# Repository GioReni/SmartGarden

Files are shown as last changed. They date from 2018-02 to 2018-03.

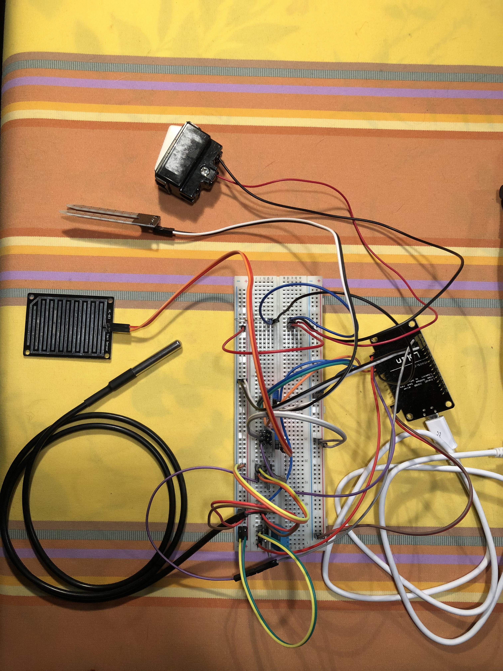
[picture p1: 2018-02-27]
foto/UnitaSensori.jpg

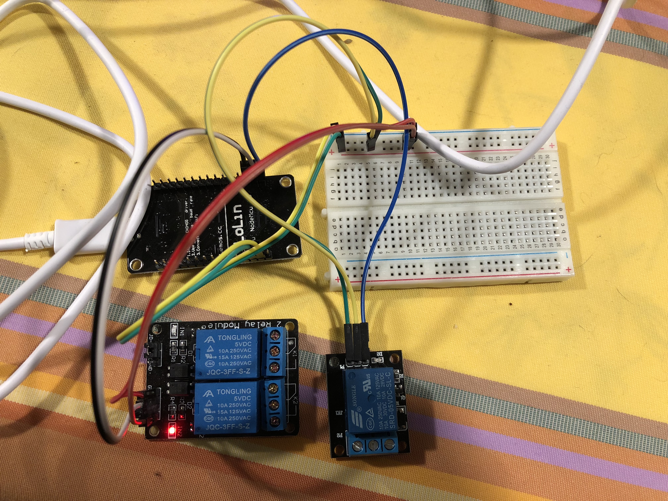
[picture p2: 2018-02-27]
foto/UnitaAttuatori.jpg

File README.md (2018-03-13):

# Progetto SmartGarden - Corso Sistemi Embedded (Università degli Studi di Milano, Anno Accademico 2017-2018)

## Autori:
Alessandro Gigliotti, Giovanni Reni 
## Board utilizzate:
NodeMCU ESP8266

### Descrizione generale:
In questo progetto, abbiamo realizzato un sistema di gestione intelligente di un piccolo orto o giardino. È presente un impianto d'irrigazione, basato sul controllo di ciò che accade e quindi di come si modifica, l'ambiente circostante. L'impianto entra infatti autonomamente in azione, quando si verificano determinate condizioni (come secchezza del terreno o assenza di pioggia), tenendo costantemente sotto controllo varie informazioni sull'aria, terra, meteo e sullo stato degli strumenti d'irrigazioni utilizzati. L'irrigazione può entrare in funzione, utilizzando una cisterna che raccoglie l'acqua piovana, oppure tramite un impianto idraulico. È altresì possibile attivare l'irrigazione anche manualmente da un utente tramite un pulsante fisico.
Le informazioni rilevate tramite i sensori in giardino, vengono inviate e visualizzate su un display, attaccato ad un'altra board, posizionato in un luogo chiuso (ad esempio in casa). Affianco al display, ci saranno anche 4 led, che segnalano la presenza/assenza di pioggia, la presenza/assenza di sole, lo stato del serbatoio pieno o vuoto. Ci sono infine 3 pulsanti fisici, posizionati accanto al display, per azionare manualmente l'irrigazione, per accendere una lampada per illuminare e un tasto per arrestare entrambe queste attività.
Inoltre il sistema sfrutta un'applicazione mobile, dalla quale sono consultabili tutte le informazioni lette dai sensori e lo stato della cisterna. Sono presenti inoltre 3 pulsanti virtuali, gemelli di quelli fisici, per azionare gli strumenti del progetto da un dispositivo. Infine l'app invia anche notifiche, relative agli eventi che accadono nel sistema.

### Descrizione dettagliata:
All'esterno, avremo il primo nodeMCU posto in prossimità del giardino. Ad esso, sono attacati tutti i sensori che utilizziamo per recepire le informazioni chiave che andremo ad utilizzare per il funzionamento generale del progetto.
I sensori utilizzati da questo nodeMCU sono:
- Temperatura e umidità dell'aria
- Temperatura e umidità della terra
- Rilevazione della pioggia
- Fotoresistore

Queste informazioni verranno costantemente tenute sotto controllo dal primo nodeMCU (file UnitaSensori.ino), che le invierà periodicamente ad un altro nodeMCU (definiamolo d'ora in avanti "controllore"), che sarà in un luogo chiuso, quindi idealmente all'interno della casa.
Le informazioni rilevate, in costante aggiornamento, saranno anche consultabili da un dispaly interno alla casa e dall'applicazione mobile.

Vicino al giardino, sarà presente una cisterna che raccoglie l'acqua piovana, che verrà usata per irrigare il giardino, nel caso in essa sia presente una sufficiente quantità d'acqua. Se la cisterna fosse vuota, il giardino verrà allora irrigato direttamente con l'acqua dell'impianto idraulico casalingo.

Tutte le decisioni, su come e quando irrigare, sono prese quindi dal nodeMCU "controllore" (file UnitaDiControllo) che abbiamo posizionato internamente alla casa e che è in comunicazione con il primo nodeMCU (UnitaSensori) di cui abbiamo parlato sopra, tramite il protocollo UDP, via WI-FI. In base alle informazioni che arrivano al controllore, quest'ultimo deciderà se azionare o meno l'irrigazione, ed in caso positivo, se sfruttare la cisterna o l'impianto idraulico casalingo. 

Abbiamo poi un terzo ed ultimo nodeMCU (UnitaAttuatori), all'esterno, a cui sono attaccati 3 relays:
- Uno per attivare l'elettrovalvola che aziona l'impianto idraulico casalingo per irrigare
- Uno per aprire la valvola dell'acqua della cisterna, per irrigare
- Uno per accendere una lampada per illuminare una pianta (quest'ultimo è azionabile solo manualmente)

Anche questo nodeMCU (UnitaAttuatori), sarà gestito dal controllore, grazie alle informazioni derivanti dal primo nodeMCU (UnitaSensori).

Descriviamo più dettagliamente il nodeMCU "controllore" (UnitaDiControllo), che sta in casa:

Esso ogni n secondi, riceve dal primo nodeMCU che controlla i sensori, i dati che ha letto.
Il controllore riceve ed elabora quindi i dati, e decide se azionare o meno i relays del terzo nodeMCU (UnitaAttuatori).
Attaccati a questo nodeMCU "controllore", abbiamo:
- Uno schermo LCD, sul quale possiamo visualizzare i dati letti dal primo nodeMCU (UnitaSensori), quindi: temperatura e umidità dell'aria, temperatura della terra, l'umidità della terra (terreni arido o umido) e infine lo stato acceso/spento dell'irrigazione e della luce della lampada.
- Quattro led: uno di colore blu, che segnala la presenza (acceso) o assenza (spento) di pioggia (funziona tramite sensore di pioggia), uno di colore giallo, che segnala la presenza (acceso) o assenza (spento) della luce del sole (funziona tramite fotoresistore), uno di colore verde, che si accende solamente quando la cisterna è piena, e uno di colore rosso che si accende solamente quando la cisterna è vuota.
un'altro, che può assumere i colori verde e rosso: verde nel caso la cisterna sia piena d'acqua, e rosso nel caso sia vuota.
- Tre bottoni: essi, fanno scattare i relays del nodeMCU esterno (UnitaAttuatori). Un bottone comanda l'apertura dell'irrigazione, uno l'accensione della lampada e l'ultimo l'arresto di entrambe queste attività.

Infine, abbiamo utilizzato un'applicazione per visualizzare le informazioni lette dal nodeMCU esterno (UnitaSensori), su un dispositivo mobile, sia Android che iOS. L'applicazione si chiama Blynk, ed è scaricabile gratuitamente dal sito https://www.blynk.cc/ e lavora con varie piattaforme, tra cui ESP8266.
Da questa applicazione mobile, una volta installata e impostato il progetto SmartGarden, sono consultabili due diversi tab.
Nel primo, chimato "sensori", sono consultabili tutte le informazioni lette dai sensori: temperatura, umidità dell'aria e temperatura della terra, attraverso delle barre circolari, con al centro il valore rilevato. Inoltre c'è un piccolo led che quando è acceso, ci informa che la cisterna è piena d'acqua.
Nel secondo tab, chiamato "relays", sono invece presenti 3 pulsanti virtuali, che assolvono alle stesse funzionalità dei pulsanti fisici gemelli, attaccati al nodeMCU controllore. Questi 3 pulsanti, una volta premuti, possono quindi far attivare l'irrigazione, accendere la lampada ed uno per eventualmente fermare queste due attività se necessario, direttamente dal proprio dispositivo mobile, sfruttando l'applicazione.
Infine quest'applicazione invia delle utili notifiche a tutti i dispositivi che la installano, se connessi con il progetto, quando si verifica l'accensione dell'impianto di irrigazione o della lampada, o l'eventuale stop di tutte le attività. Sarà così possibile vedere tramite la notifica, ad esempio l'orario a cui si è accesa l'irrigazione in maniera automatica, direttamente dal proprio dispositivo. 

### Lista completa componenti utilizzati:
- 1 Sonda sensore di temperatura waterproof DS18B20
- 1 Rain sensor HL38
- 1 Modulo sensore umidità terra - igrometro YL-69
- 1 KY-018 modulo Fotodiodo
- 1 Elettrovalvola
- 1 Interruttore a galleggiante sensore livello liquido di accio inox RG-1075S
- Pompa acqua 220V
- 1 5V 1-Channel Relay Module
- 1 5V 2-Channel Relay Module
- 3 Pulsanti
- 1 resistenza da 100 Ohms
- 1 resistenza da 220 Ohms
- 1 resistenza da 1 kOhm
- 1 resistenza da 4.7 kOhms
- 5 resistenze da 10 kOhms
- 4 LED (Red, Green, Blue, Yellow)
- 1 KY-015 Sensore di temperatura e umidità dell'aria (DHT11)
- 1 Modulo LCD 20x4 I2C/TWI

## Lista librerie utilizzate:
- Blynk Library (app: https://github.com/blynkkk/blynk-library/releases/tag/v0.5.1)
- ESP8266WiFi
- WiFiUdp
- LiquidCrystal_I2C
- SimpleTimer
- SPI
- Adafruit_Sensor
- DHT
- DHT_U
- OneWire
- DallasTemperature

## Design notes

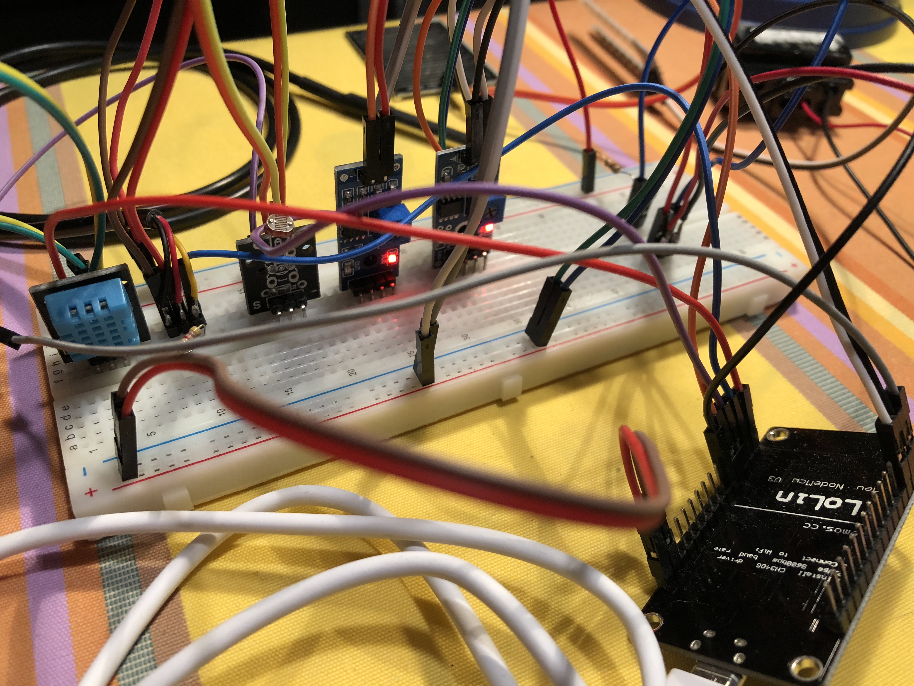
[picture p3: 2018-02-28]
foto/UnitaSensori2.jpg

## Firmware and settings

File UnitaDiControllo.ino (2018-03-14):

/*
 *  Copyright 2018 Giovanni Reni & Alessandro Gigliotti
 * 
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
 * SmartGarden1.0 is distributed in the hope that it will be useful,
 * but WITHOUT ANY WARRANTY; without even the implied warranty of
 * MERCHANTABILITY or FITNESS FOR A PARTICULAR PURPOSE. See the
 * GNU General Public License for more details.
 * You should have received a copy of the GNU General Public License
 * along with this program. If not, see <http://www.gnu.org/licenses/>.
 */

#define BLYNK_PRINT Serial

#include <ESP8266WiFi.h>
#include <WiFiUdp.h>
#include <LiquidCrystal_I2C.h>
#include <SimpleTimer.h>
#include <SPI.h>
#include <BlynkSimpleEsp8266.h>

LiquidCrystal_I2C lcd(0x3F, 20, 4);

char auth[] = "****"; //Blynk app

WiFiUDP Udp;
unsigned int localUdpPort = 4210;                 //cambiare con porta che si vuole assegnare a questo NodeMcu (UnitaDiControllo)
char incomingPacket[UDP_TX_PACKET_MAX_SIZE];

IPAddress ip(192, 168, 1, 35);                     //cambiare con indirizzo IP che si vuole assegnare a questo NodeMcu (UnitaDiControllo)
IPAddress gateway(192, 168, 1, 254);               //cambiare con gateway della propria rete
IPAddress subnet(255, 255, 255, 0);                //cambiare con subnet della propria rete

const char* ssid = "ArduinoAfternoon";                     //cambiare con ssid della propria Wi-Fi
const char* password = "***";                 	   //cambiare con password della propria Wi-Fi

char * luceOff = "L0";                            //comando spegni luce
char * luceOn = "L1";                             //comando accendi luce
char * pumpOff = "P0";                            //comando spegni pompa
char * pumpOn = "P1";                             //comando accendi pompa
char * evOff = "E0";                              //comando spegni elettrovalvola
char * evOn = "E1";                               //comando accnedi elettrovalvola

int tempoIrrPuls = 10;                            //cambiare a piacere se si vuole modificare tempo (in sec.) innaffiata con pulsante
int tempoIrrAuto = 300; //300 sec <--> 5 min      //cambiare a piacere se si vuole modificare tempo (in sec.) innaffiata automatica
int tempoLucePuls = 10;                           //cambiare a piacere se si vuole modificare tempo (in sec.) illuminazione con pulsante
int tempoLuceAuto = 300;                          //cambiare a piacere se si vuole modificare tempo (in sec.) illuminazione automatica

//indirizzo IP + Porta NodeMcu ATTUATORE
char * indirizzoRelaisGiardino = "192.168.1.36";  //cambiare con indirizzo IP del proprio NodeMcu attuatore
int portaRelaisGiardino = 4240;                   //cambiare con porta del proprio NodeMcu attuatore

//pin LED pioggia
int pinGiallo = D5;
int pinBlu = D6;

//pin LED serbatoio
int pinVerde =  D4;
int pinRosso = D7;

//pin bottone lucePianta
int bottoneLuce = D8;

//pin bottone pompa
int bottonePompa = D0;

//pin bottone STOP
int bottoneStop = A0;

//variabile pioggia (0 --> NON piove)
int pioggia = 0;
//variabile serbatoio (0 --> vuoto)
int serbatoio = 0;
//variabile umidita' terra
int umiditaTerra;
//variabile temperatura terra
double temperaturaTerra;
//variabile temperatura aria
int temperatura;
//variabile luce env.
int luce;
//variabile umidita aria
int umidita;
//variabile tipo irrigatore
char irrigatore [] = "P";
//variabile tipo luce
char illuminazione [] = "L";
//variabile pulsante irrigazione temporanea
int letturaPulsanteAcqua = LOW;
//variabile pulsante illuminazione temporanea
int letturaPulsanteLuce = LOW;
//variabile pulsante STOP
int letturaPulsanteStop = 0;
//variabile comando
char comando [UDP_TX_PACKET_MAX_SIZE];
//variabile per convertire gli interi
char temp [15];
//variabile temporanea numero
int numero;


//######################################################################################## FUNCTIONS 1 ########################################################################################
void printIllOff() {
  lcd.setCursor(0,3);
  lcd.print("Luce:");
  lcd.print("OFF   ");
}

void printAcquaOff() {
  lcd.setCursor(11,3);
  lcd.print("Acqua:");
  lcd.print("OFF");
}

void printIllIrrOff() {
  printIllOff();
  printAcquaOff();
}


//########################################################################################### SETUP ###########################################################################################
void setup() {
  //pin LED pioggia
  pinMode(pinGiallo, OUTPUT);
  pinMode(pinBlu, OUTPUT);

  //pin bottoni STOP, IRRIGAZIONE, LUCE
  pinMode(bottonePompa, INPUT);
  pinMode(bottoneStop, INPUT);
  pinMode(bottoneLuce, INPUT);
  
  //pin LED serbatoio
  pinMode(pinVerde, OUTPUT);
  pinMode(pinRosso, OUTPUT);

  Blynk.begin(auth, ssid, password);
  
  Serial.begin(9600);
  Serial.println();
  Serial.printf("Connecting to %s ", ssid);
  //WiFi.mode(WIFI_STA);
  WiFi.config(ip, gateway, subnet);
  WiFi.begin(ssid, password);
  while (WiFi.status() != WL_CONNECTED)
  {
    delay(500);
    Serial.print(".");
  }
  Serial.println(" connected");

  //Serial.print("Indirizzo IP UnitaDiControllo: ");
  //Serial.pritnln(WiFi.localIP());
  Udp.begin(localUdpPort);
  Serial.printf("Now listening at IP %s, UDP port %d\n", WiFi.localIP().toString().c_str(), localUdpPort);

  //settaggio display LCD
  lcd.begin(20,4);
  lcd.init();
  lcd.backlight();

  printIllIrrOff();
}


//######################################################################################## FUNCTIONS 2 ########################################################################################
void sendPacket(char pacchetto [8], char * indirizzo, int porta) {
  Udp.beginPacket(indirizzo, porta);
  Udp.write(pacchetto);
  Udp.endPacket();
}

void printTemp(int i) {
  lcd.setCursor(0,0);
  lcd.print("Temp:");
  lcd.print(String(i));
  lcd.print((char)223);
  lcd.print("C");
}

void printHum(int i) {
  lcd.print("  Umid:");
  lcd.print(String(i));
  lcd.print("%");
}

void printTempTerra(double d) {
  lcd.setCursor(0,1);
  lcd.print("Temp Terra:");
  lcd.print(String(d));
  lcd.print((char)223);
  lcd.print("C");
}

void printUmidTerra(int i) {
  lcd.setCursor(0,2);
  if(i==1) {
     lcd.print("Terreno Umido");
   }
   else if(i==0) {
     lcd.print("Terreno Arido");
   }
}

void ledPioggia(int i) {
  if(i==1) {
     digitalWrite(pinBlu, HIGH);
     analogWrite(pinGiallo, LOW);
   }
   else if(i==0) {
     digitalWrite(pinBlu, LOW);
     analogWrite(pinGiallo, HIGH);
   }
}

void ledSerbatoio(int i) {
  if(i==0) {
    digitalWrite(pinVerde, LOW);
    digitalWrite(pinRosso, HIGH);
   }
   else {
     digitalWrite(pinVerde, HIGH);
     digitalWrite(pinRosso, LOW);
   }
}

void spegniTutto() {
  sendPacket(luceOff, indirizzoRelaisGiardino, portaRelaisGiardino);
  sendPacket(pumpOff, indirizzoRelaisGiardino, portaRelaisGiardino);
  sendPacket(evOff, indirizzoRelaisGiardino, portaRelaisGiardino);
}

void clearArray(char lista[UDP_TX_PACKET_MAX_SIZE]) {
  for (int i = 0; i< sizeof(lista); i++) {
    lista[i]=(char)0;
  } 
}

void printIllOn() {
  lcd.setCursor(0,3);
  lcd.print("Luce:");
  lcd.print("ON    ");
}

void printAcquaOn() {
  lcd.setCursor(11,3);
  lcd.print("Acqua:");
  lcd.print("ON ");
}

//lettura pulsante acqua con Blynk app
BLYNK_WRITE(V5) {
  int pinValue = param.asInt();
  if(pinValue==1){
    letturaPulsanteAcqua = HIGH;
  }
}

//lettura pulsante lampada con Blynk app
BLYNK_WRITE(V6) {
  int pinValue = param.asInt();
  if(pinValue==1){
    letturaPulsanteLuce = HIGH;
  }
}

//lettura pulsante stop con Blynk app
BLYNK_WRITE(V7) {
  int pinValue = param.asInt();
  if(pinValue==1){
    letturaPulsanteStop = 1024;
  }
}

//########################################################################################### MAIN ###########################################################################################
void loop() {
  String ricevuta;

  Blynk.run();
  
  //ricezione lettura sensori da UnitaSensori and UnitaAttuatori
  delay(100);
  int packetSize = Udp.parsePacket();
  
  if (packetSize > 0) {
    //Serial.printf("Received %d bytes from %s, port %d\n", packetSize, Udp.remoteIP().toString().c_str(), Udp.remotePort());
    Udp.read(incomingPacket, packetSize);
    ricevuta = String(incomingPacket);
      //ricezione dati sensori da UnitaSensori
      if (ricevuta.indexOf("T") != -1) {
        temperatura = ricevuta.substring(ricevuta.indexOf("T")+1, ricevuta.indexOf("H")).toInt();
        umidita = ricevuta.substring(ricevuta.indexOf("H")+1, ricevuta.indexOf("TH")).toInt();
        temperaturaTerra = atof(ricevuta.substring(ricevuta.indexOf("TH")+2, ricevuta.indexOf("R")).c_str());
        pioggia = ricevuta.substring(ricevuta.indexOf("R")+1, ricevuta.indexOf("L")).toInt();
        luce = ricevuta.substring(ricevuta.indexOf("L")+1, ricevuta.indexOf("HE")).toInt();
        umiditaTerra = ricevuta.substring(ricevuta.indexOf("HE")+2, ricevuta.indexOf("S")).toInt();
        serbatoio = ricevuta.substring(ricevuta.indexOf("S")+1).toInt();
        printTemp(temperatura);
        printHum(umidita);
        printTempTerra(temperaturaTerra);
        printUmidTerra(umiditaTerra);
        ledPioggia(pioggia);
        ledSerbatoio(serbatoio);
      }

      //notifica di spegnimento acqua da UnitaAttuatori
      else if (ricevuta.indexOf("W") != -1) {
        printAcquaOff();
      }
      //notifica di spegnimento luce da UnitaAttuatori
      else if (ricevuta.indexOf("i") != -1) {
        printIllOff();
      }
     Serial.printf("UDP packet contents: %s\n", incomingPacket);
     clearArray(incomingPacket);
  }

  //lettura pulsante STOP
  if (letturaPulsanteStop < 1024) {
    letturaPulsanteStop = analogRead(bottoneStop);
  }

  //lettura pulsante pompa
  if (letturaPulsanteAcqua == LOW) {
    letturaPulsanteAcqua = digitalRead(bottonePompa);
  }

  //lettura pulsante luce
  if (letturaPulsanteLuce == LOW) {
    letturaPulsanteLuce = digitalRead(bottoneLuce);
  }

  if (pioggia == 1 || letturaPulsanteStop == 1024) {
    spegniTutto();
    printIllIrrOff();
  }
  else {
    if (serbatoio == 1 && strcmp(irrigatore,"E")==0) {
      strncpy(irrigatore, "P", 3);
      sendPacket(irrigatore, indirizzoRelaisGiardino, portaRelaisGiardino); 
    }
    else if (serbatoio == 0 && strcmp(irrigatore,"P")==0) {
           strncpy(irrigatore, "E", 3);
           sendPacket(irrigatore, indirizzoRelaisGiardino, portaRelaisGiardino);  
    }

    //pulsante irrigazione premuto <--> HIGH pressed, LOW released
    if (letturaPulsanteAcqua == HIGH) {
      numero = 1;
      clearArray(temp);
      clearArray(comando);
      strncpy(comando, irrigatore, 1);
      itoa(numero, temp, 10);
      strcat(comando, temp);
      itoa(tempoIrrPuls, temp, 10);
      strcat(comando, temp);
      sendPacket(comando, indirizzoRelaisGiardino, portaRelaisGiardino);
      printAcquaOn();
    }
    
    //condizioni di secco
    if ((umiditaTerra == 0) && (temperaturaTerra > 8.0) && (temperatura > 5.0) && (luce > 950) && (umidita < 80)) {
      numero = 1;
      clearArray(temp);
      clearArray(comando);
      strncpy(comando, irrigatore, 1);
      itoa(numero, temp, 10);
      strcat(comando, temp);
      itoa(tempoIrrAuto, temp, 10);
      strcat(comando, temp);
      sendPacket(comando, indirizzoRelaisGiardino, portaRelaisGiardino);
      printAcquaOn(); 
    }

    //pulsante luce premuto <--> HIGH pressed, LOW released
    if(letturaPulsanteLuce == HIGH) {
      numero = 1;
      clearArray(temp);
      clearArray(comando);
      strncpy(comando, illuminazione, 1);
      itoa(numero, temp, 10);
      strcat(comando, temp);
      itoa(tempoLucePuls, temp, 10);
      strcat(comando, temp);
      sendPacket(comando, indirizzoRelaisGiardino, portaRelaisGiardino);
      printIllOn();
    }

    //condizioni di illuminazione
    if ((temperaturaTerra <= 8.0) && (temperatura <= 5) && (luce >= 950)) {
      numero = 1;
      clearArray(temp);
      clearArray(comando);
      strncpy(comando, illuminazione, 1);
      itoa(numero, temp, 10);
      strcat(comando, temp);
      itoa(tempoLuceAuto, temp, 10);
      strcat(comando, temp);
      sendPacket(comando, indirizzoRelaisGiardino, portaRelaisGiardino);
      printIllOn();
    }
  }

  //reset pulsanti Blynk app
  letturaPulsanteAcqua = LOW;
  letturaPulsanteLuce = LOW;
  letturaPulsanteStop = 0;
  
}

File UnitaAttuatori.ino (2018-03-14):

/*
 *  Copyright 2018 Giovanni Reni & Alessandro Gigliotti
 * 
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
 * SmartGarden1.0 is distributed in the hope that it will be useful,
 * but WITHOUT ANY WARRANTY; without even the implied warranty of
 * MERCHANTABILITY or FITNESS FOR A PARTICULAR PURPOSE. See the
 * GNU General Public License for more details.
 * You should have received a copy of the GNU General Public License
 * along with this program. If not, see <http://www.gnu.org/licenses/>.
 */


#define BLYNK_PRINT Serial
#include <BlynkSimpleEsp8266.h>
#include <ESP8266WiFi.h>
#include <WiFiUdp.h>

WiFiUDP Udp;
unsigned int localUdpPort = 4240;                                         //cambiare con porta del proprio NodeMcu UnitaAttuatori
char incomingPacket[UDP_TX_PACKET_MAX_SIZE];

IPAddress ip(192, 168, 1, 36);                                            //cambiare con indirizzo IP che si vuole assegnare a questo NodeMcu (UnitaAttuatori)
IPAddress gateway(192, 168, 1, 254);                                      //cambiare con gateway della propria rete
IPAddress subnet(255, 255, 255, 0);                                       //cambiare con subnet della propria rete

const char* ssid = "ArduinoAfternoon";                                            //cambiare con ssid della propria Wi-Fi
const char* password = "***"; 	                                          //cambiare con password della propria Wi-Fi

char * indirizzoUnitaDiControllo = "192.168.1.35";                        //cambiare con indirizzo IP del proprio NodeMcu UnitaDiControllo
int portaUnitaDiControllo = 4210;                                         //cambiare con porta del proprio NodeMcu UnitaDiControllo

int lucePianta = D0;
int relaisPompa = D1;
int relaisElettrovalvola = D2;

//variabile spegni acqua
char spegniAcqua[] = "Water";
//variabile spegni luce
char spegniLuce[] = "Light";

int tempoInizioIrr = 0;
int tempoDurataIrr = 0;
boolean innaffia = false;
boolean illumina = false;
int tempoInizioIll = 0;
int tempoDurataIll = 0;

char auth [] = "****";


//########################################################################################### SETUP ###########################################################################################
void setup() {
  Blynk.begin(auth, ssid, password);
  //settaggio pin luce pianta
  pinMode(lucePianta, OUTPUT);
  digitalWrite(lucePianta, LOW); //setta a OFF la luce, inizialmente

  //settaggio pin pompa
  pinMode(relaisPompa, OUTPUT);
  digitalWrite(relaisPompa, HIGH); //setta a OFF la pompa, inizialmente

  //settaggio pin elettrovalvola
  pinMode(relaisElettrovalvola, OUTPUT);
  digitalWrite(relaisElettrovalvola, HIGH); //setta a OFF l'elettrovalvola, inizialmente
  
  Serial.begin(9600);
  Serial.println();
  Serial.printf("Connecting to %s ", ssid);
  //WiFi.mode(WIFI_STA);
  WiFi.config(ip, gateway, subnet);
  WiFi.begin(ssid, password);
  while (WiFi.status() != WL_CONNECTED)
  {
    delay(500);
    Serial.print(".");
  }
  Serial.println(" connected");

  //Serial.print("Indirizzo IP UnitaAttuatori: ");
  //Serial.pritnln(WiFi.localIP());
  Udp.begin(localUdpPort);
  Serial.printf("Now listening at IP %s, UDP port %d\n", WiFi.localIP().toString().c_str(), localUdpPort);
}


//######################################################################################### FUNCTIONS #########################################################################################
void sendPacket(char pacchetto [8], char * indirizzo, int porta) {
  Udp.beginPacket(indirizzo, porta);
  Udp.write(pacchetto);
  Udp.endPacket();
}


//########################################################################################### MAIN ###########################################################################################
void loop() {
  Blynk.run();
  //attesa richiesta scatto relais
  String ricevuta;
  int packetSize = Udp.parsePacket();
  if (packetSize > 0) {
   //receive incoming UDP packets
   //Serial.printf("Received %d bytes from %s, port %d\n", packetSize, Udp.remoteIP().toString().c_str(), Udp.remotePort());
   Udp.read(incomingPacket, packetSize);
   Serial.printf("UDP packet contents: %s\n", incomingPacket);
   ricevuta = String(incomingPacket);
    
   //HIGH su relais pompa + elettrovalvola, la spegne
   //LOW su relais luce, la spegne
   if (ricevuta.indexOf("L0") != -1) {
      digitalWrite(lucePianta, LOW);
      illumina = false;
      tempoDurataIll = 0;
      Blynk.notify("L'impianto di irrigazione e di illuminazione si sono arrestati per STOP o PIOGGIA");
   }
   if (ricevuta.indexOf("P0") != -1) {
      digitalWrite(relaisPompa, HIGH);
      innaffia = false;
      tempoDurataIrr = 0;
   }
   if (ricevuta.indexOf("E0") != -1) {
      digitalWrite(relaisElettrovalvola, HIGH);
      innaffia = false;
      tempoDurataIrr = 0;
   }
   else if ((ricevuta.indexOf("P1") != -1) && innaffia == false) {
      innaffia = true;
      tempoInizioIrr = millis();
      tempoDurataIrr = tempoInizioIrr + (ricevuta.substring(ricevuta.indexOf("P1")+2).toInt()*1000);
      digitalWrite(relaisPompa, LOW);
      Blynk.notify("L'impianto di irrigazione si e' acceso");
    }
    else if ((ricevuta.indexOf("E1") != -1) && innaffia == false) {
      innaffia = true;
      tempoInizioIrr = millis();
      tempoDurataIrr = tempoInizioIrr + (ricevuta.substring(ricevuta.indexOf("E1")+2).toInt()*1000);
      digitalWrite(relaisElettrovalvola, LOW);
      Blynk.notify("L'impianto di irrigazione si e' acceso");
    }
    else if (ricevuta.indexOf("L1") != -1 && illumina == false) {
      illumina = true;
      tempoInizioIll = millis();
      tempoDurataIll = tempoInizioIll + (ricevuta.substring(ricevuta.indexOf("L1")+2).toInt()*1000);
      digitalWrite(lucePianta, HIGH);
      Blynk.notify("L'impianto di illuminazione si e' acceso");
    }
    else if (ricevuta.indexOf("E") != -1 && innaffia == true) {
      digitalWrite(relaisPompa, HIGH);
      digitalWrite(relaisElettrovalvola, LOW);
    }
    else if (ricevuta.indexOf("P") != -1 && innaffia == true) {
      digitalWrite(relaisPompa, LOW);
      digitalWrite(relaisElettrovalvola, HIGH);
    }

  } //chiusura if(packetSize > 0)

    if (tempoDurataIrr != 0 && millis() > tempoDurataIrr) {
      digitalWrite(relaisPompa, HIGH);
      digitalWrite(relaisElettrovalvola, HIGH);
      innaffia = false;
      sendPacket(spegniAcqua, indirizzoUnitaDiControllo, portaUnitaDiControllo);
      tempoDurataIrr = 0;
      Blynk.notify("L'impianto di irrigazione si e' spento automaticamente");
    }
    if(tempoDurataIll != 0 && millis() > tempoDurataIll) {
      digitalWrite(lucePianta, LOW);
      illumina = false;
      sendPacket(spegniLuce, indirizzoUnitaDiControllo, portaUnitaDiControllo);
      tempoDurataIll = 0;
      Blynk.notify("L'impianto di illuminazione si e' spento automaticamente");
    }
    
}

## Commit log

2018-02-28 Add files via upload
    Implementate delle funzionalità con l'applicazione mobile Blynk, che visualizza varie informazioni sui sensori (temperatura aria, umidità terra, temperatura terra e serbatoio pieno/vuoto) e permette 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
2018-03-12 interruttore luce + attivazione auto
    - interruttore luce + attivazione auto luce restano disabilitati fino al termine del ciclo di accensione
    - alcuni commenti sistemati

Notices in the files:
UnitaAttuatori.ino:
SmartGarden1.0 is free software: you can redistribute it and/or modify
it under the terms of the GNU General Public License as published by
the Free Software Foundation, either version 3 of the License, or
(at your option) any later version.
